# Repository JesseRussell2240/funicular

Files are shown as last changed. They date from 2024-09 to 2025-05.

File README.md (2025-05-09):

# funicular
Selfdriving R-pi code

**Establishing SSH From Laptop To Rpi**
1. Get IP of RPI should be like 192.168.#.###

2. Enable SSH on the Rpi
   -Open Terminal on the Rpi and type **"sudo raspi-config"** in the configuration menu go to "3. Interface      Options" and enable SSH
   -In CMD on laptop type "ssh rpi@rpi ip address found in step one" Ex. **"ssh rpi@192.168.#.###"**
   -If prompted with "WARNING: REMOTE HOST IDENTIFICATION HAS CHANGED" it means you have an existing key under that IP address, type "ssh-keygen -R ip address found in step one" Ex. **"ssh-keygen -R 192.168.#.###"** This will clear that key
   -Now try **"ssh rpi@192.168.#.###"** again, when prompted to continue connected type **"yes"**
   -When prompted for the password, enter the Rpis password you set when configuring Ex **"rpi_password"**
   -SSH should now be established

**Installing OpenCV in Terminal on Rpi**
1. In Terminal **"pip install opencv-python --break-system-package"**

**Installing PiCamera in Terminal on Rpi**
1. In Terminal **"pip install picamera --break-system-package"**

**Camera Unit Testing instructions**
**this needs confirming**
1. pip install picamera opencv-python

2. run unit testing code - python test_camera_module.py
After this is running you should see a window with a live camera feed.Type 'q' to exit.

**Preception unit testing instructions**
**This needs confirming**
1. pip install opencv-python numpy

2. run unit testing code - python test_perception_module.py
preception also has a main to test preception and cameras joint integration. Ensure camera module is successfull prior to moving on to preception.

This is to install flask and other for R-Pi server hosting website to control and recive video remotly
pip install flask flask-socketio opencv-python

ENSURE FLASK SERVER IS NOT IN DEBUG OR LIVESTREAM WILL NOT WORK

**Funicular Readme**

**------------------------------Python---------------------------------**

**App.py**<br>
App.py enables the flask-based web server and is responsible for all the data displayed on the web server and the controls within the web server. App.py sets up the flask server, enables and handles the frames of the Module 3 Wide PiCam (dependent on Autonomous or Manual Mode), enables, reads and graphs the BNO08X 9-DOF sensor data via I2C, and handles the flask routes for the webserver (landing_page, auto_mode, manual_mode, 3d_model, live_video & graphs)

**Machine Learning**<br>
For our ML model, we started by taking 100s of photos of our cones in various settings, configurations, and lighting, as well as some photos without cones. Once we had roughly 250 photos, we uploaded them to Roboflow (https://roboflow.com/), where we created our object class, cones, and manually selected the pixels containing cones. Once this was done, we used Roboflow to generate copies of each photo rotated, flipped, greyscales and inverted, bringing our total photos to about 1600. Once completed, we downloaded our dataset and yaml file. With our yaml created file, we then used the YOLO model 8 in Python to train on our dataset, running 100 epochs. Once this was completed, we received our best.pt file. Follow this tutorial to convert the .pt to a .hef and run it on Rpi’s Hailo Modules. https://www.youtube.com/watch?v=7pgSFgqo8gY
<br>
<br>
**-----------------------------Embedded--------------------------------**

**UART3.c**<br>
Sets up UART interface on USART3 for receiving motor control commands from an external Raspberry Pi. It handles the reception of direction, duty cycle, and turning values, parses them, and adjusts motor behaviour accordingly. The code includes an interrupt-driven approach for receiving data and sending responses back, allowing for continuous operation with real-time motor adjustments.

**DriveMotor_Breifing.c**<br>
The code configures and controls drive motors by setting up GPIO pins and timers to manage motor speed and direction. It uses PWM signals generated by Timer 8 for precise speed control and toggles GPIO pins for motor direction (forward, backward, or stop). The code provides functions to adjust both the speed (duty cycle) and direction of the turning and rear motors, allowing for real-time motor control in a robotic or motorized system.

**LimitSwitch.c**<br>
The code initializes and configures two limit switches (we run in series to PC5) to pins PC5 and PC6 of the STM32 microcontroller. The code triggers interrupts on the rising edge of the signals from these limit switches. When an interrupt is detected, the interrupt handler stops the turning motor (via the SetMotor function) and sets a flag indicating that a limit switch has been triggered. The interrupt flags are then cleared to allow further interrupts to be processed.

**Homing.c**<br>
The code implements a homing function for the turning motor using the limit switches and encoder to find the midpoint between two limit positions. It moves the motor left until the first limit switch is triggered, the encoder is reset, and the motor is reversed right to move towards the second limit switch. Once triggered, the motor is stopped, and the encoder value is recorded as the full turn value. The motor is then moved back toward the first limit switch, which continues until it reaches the midpoint of the full turn based on the encoder value. Once the midpoint is reached, the motor is stopped. The homing process ensures precise positioning with the help of the limit switches and encoder feedback.

**Encoder.c**<br>
The code initializes and configures the encoder interface using the TIM2 peripheral for motor pulse tracking. It enables clocks for the necessary GPIO ports and configures PA0 and PA1 as alternate function pins for TIM2 channels. TIM2 is set to encoder mode, which counts rising and falling edges from the input channels (CH1 and CH2). The encoder data is tracked through the TIM2 counter, which increments or decrements based on the motor's rotation direction. The encoder interface provides real-time position feedback, allowing motor position tracking.

**Pinouts**<br>
**Motors**<br>
PC2: Turning Motor Forward direction control (+ terminal)<br>
PC3: Turning Motor Reverse direction control (- terminal)<br>
PC10: Turning Motor PWM for speed control<br>
PB12: Rear Left Motor Forward direction control (+ terminal)<br>
PC4: Rear Left Motor Reverse direction control (- terminal)<br>
PC11: Rear Left Motor PWM for speed control<br>
PC1: Rear Right Motor Forward direction control (+ terminal)<br>
PC0: Rear Right Motor Reverse direction control (- terminal)<br>
PC12: Rear Right Motor PWM for speed control<br>

**Limit Switches**<br>
PC5: Left & right limit switch (wired in series) interrupts<br>

**Encoder**<br>
PA0: Encoder Channel 1 Pulse Input<br>
PA1 Encoder Channel 2 Pulse Input<br>

**UART**<br>
PB10: UART Transmit<br>
PB11: UART Receive<br>

**----------------------------Bill of Materials--------------------------**

**Raspberry Pi** (Tested on 8gb Rpi 5) https://www.pishop.ca/product/raspberry-pi-5-8gb/ 

**Raspberry Pi Ai Hat** https://www.pishop.ca/product/raspberry-pi-ai-hat-13-tops/ 

**Module 3 Wide PiCam** https://www.pishop.ca/product/raspberry-pi-camera-module-3-wide/

**BNO08X 9-DOF Sensor** https://www.adafruit.com/product/4754

**STM32F303RE** https://www.digikey.com/en/products/detail/stmicroelectronics/NUCLEO-F303RE/5052640 

**Quadrate Encoder Motor** https://www.amazon.ca/CHF-GM12-N20VA-Encoder-Reducer-Carbon-Popular/dp/B0DCRHDT71?th=1

**TT Motors** (Can buy from various sites, usually some good bundles on Amazon)

**Wheels & Tires** https://www.amazon.ca/SD-Tires-Off-Road-Wheel-Spokes/dp/B01DU1Q2Z2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

**Limit Switches** (Any normally open snap-action limit switches will do)

**Battery** (Any battery able to supply ~5A will do) 

**Voltage Regulators** (Any voltage regular capable of doing the supplied battery voltage down to 5V for the Rpi and 10V for the TT motors will do, we used) https://www.amazon.ca/dp/B076H3XHXP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 

TO DO
1. set up PI to host network
2. intgrate ML main and Flask server main
3. Get live cone frames into server
4. clean up GIT
5. Boot config for powerup booting Venv and server

**--------------------------------------------------------------------------------------------------------------------------<br>
-----------------------------------------------------Funicular By-------------------------------------------------------<br>
----------------------------------------------------Hayden & Jesse----------------------------------------------------<br>
----------------------------------------------------------2024----------------------------------------------------------<br>
--------------------------------------------------------------------------------------------------------------------------**

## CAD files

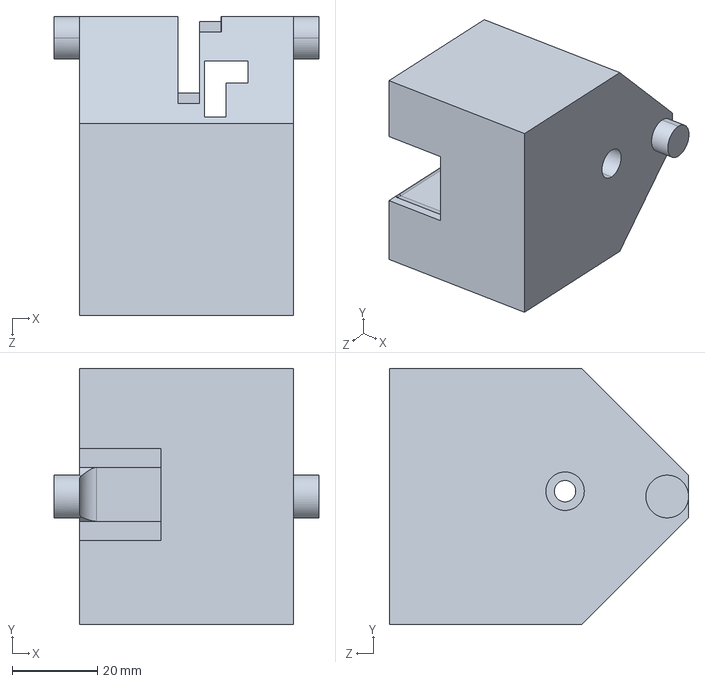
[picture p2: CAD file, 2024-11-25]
CAD/Solidworks/Print day 2/steering gearbox assembly.STEP
62.0 x 60.0 x 70.0 mm

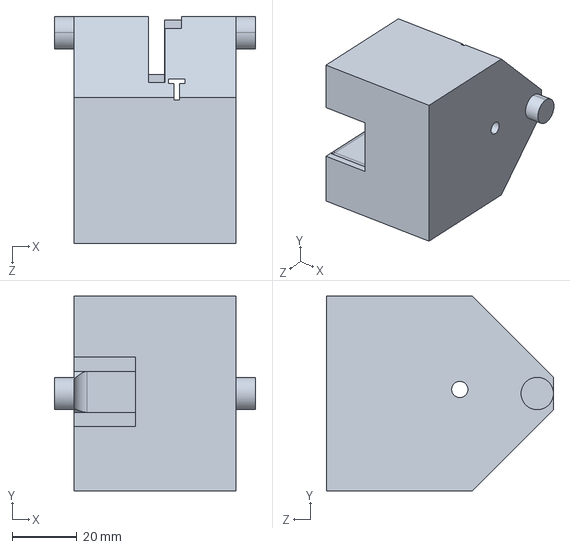
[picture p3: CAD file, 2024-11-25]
CAD/Solidworks/steering gearbox assembly.STEP
62.0 x 60.0 x 70.0 mm

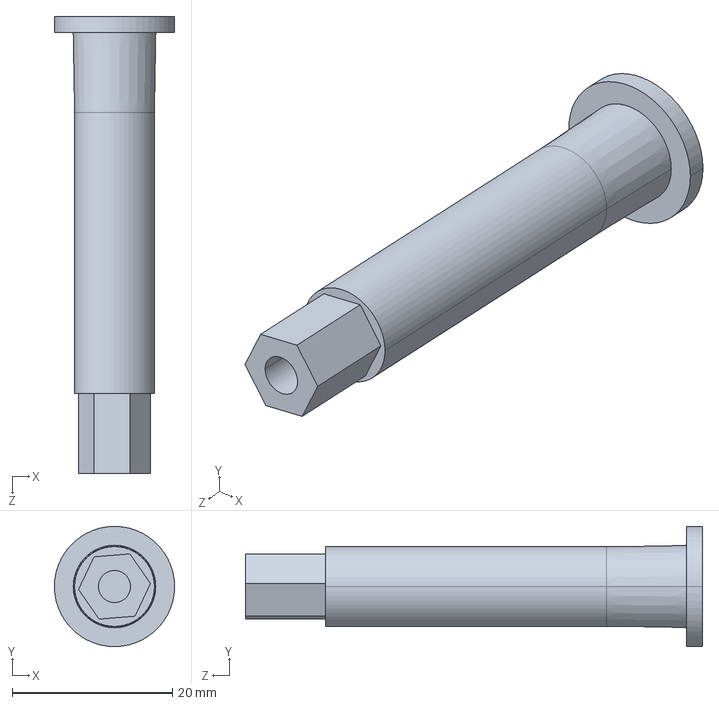
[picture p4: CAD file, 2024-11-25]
CAD/Solidworks/print day 2.2/rear bearing axel.STEP
15.0 x 15.0 x 57.0 mm

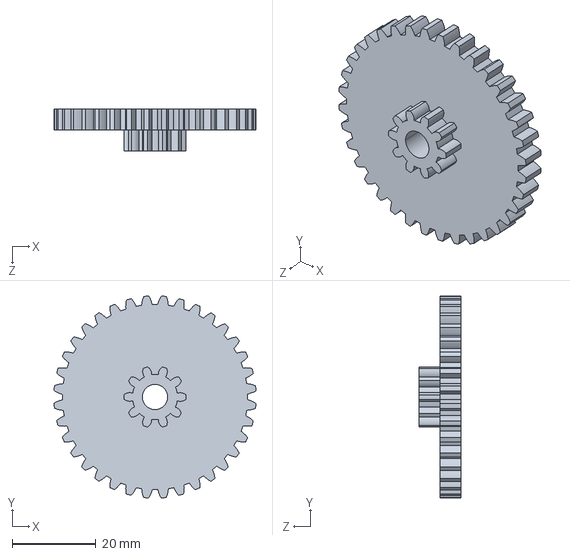
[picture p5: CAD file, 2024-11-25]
CAD/Solidworks/Print day 2/Reduction Gear.STEP
48.2 x 48.2 x 10.0 mm

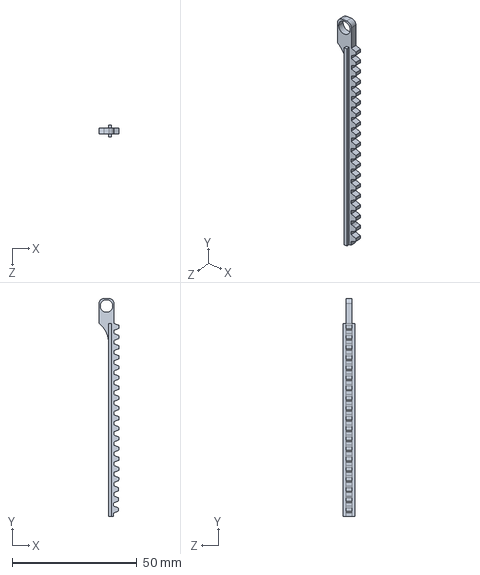
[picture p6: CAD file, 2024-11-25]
CAD/Solidworks/Rack Slidder.STEP
8.00 x 87.5 x 5.00 mm

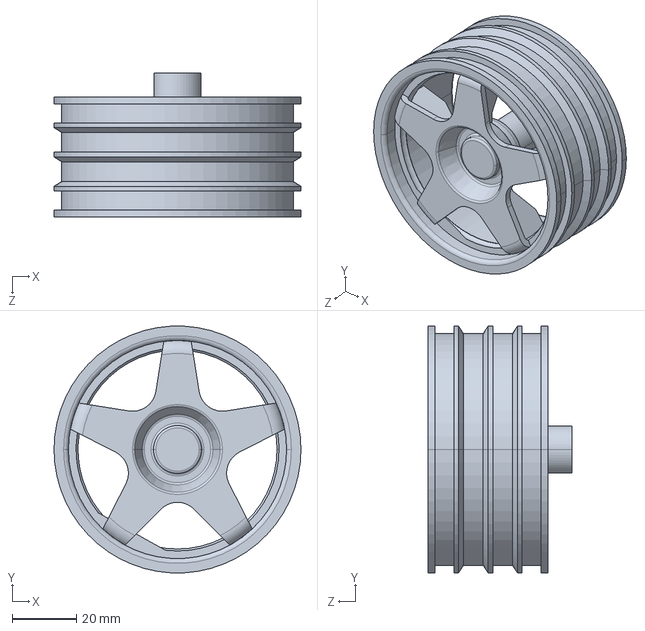
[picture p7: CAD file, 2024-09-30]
CAD/Solidworks/TireWheel/Rim.STEP
77.1 x 77.0 x 45.0 mm

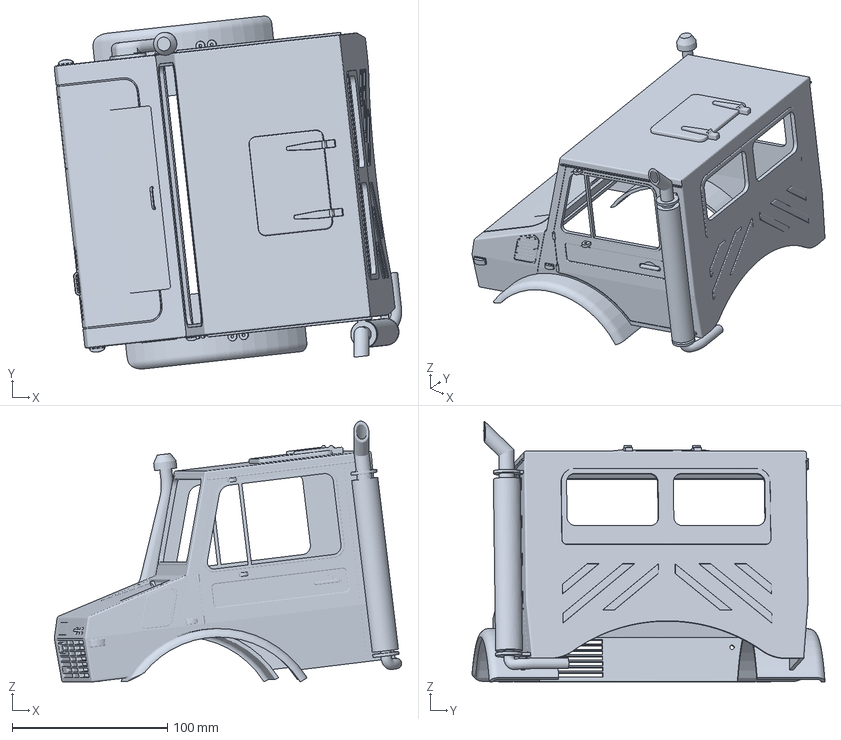
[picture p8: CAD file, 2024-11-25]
CAD/Solidworks/Unimog/Unimog.3mf
224.0 x 227.6 x 168.1 mm

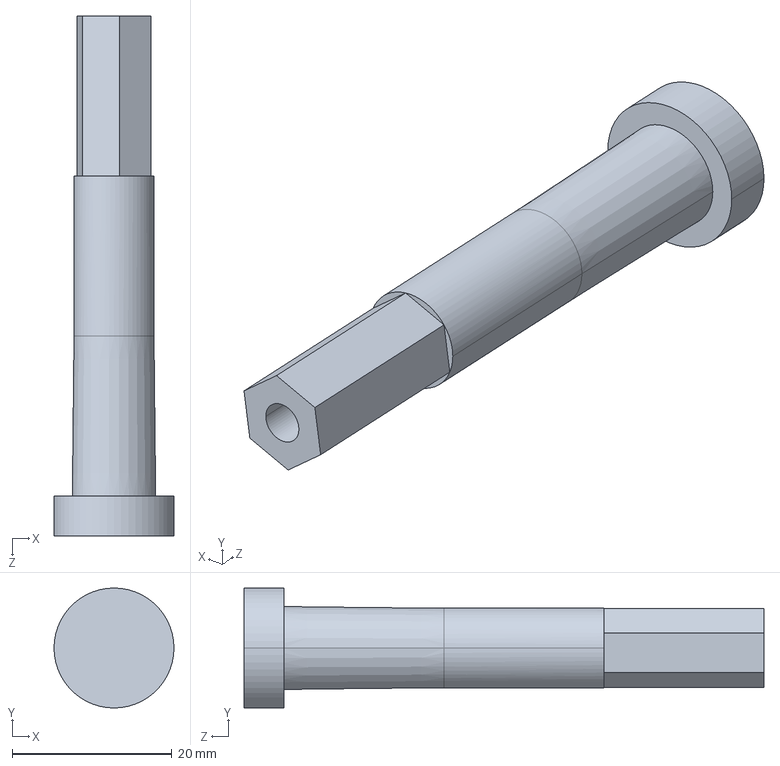
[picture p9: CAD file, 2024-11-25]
CAD/Solidworks/print day 2.2/front bearing axel part 1.STEP
15.0 x 15.0 x 65.0 mm

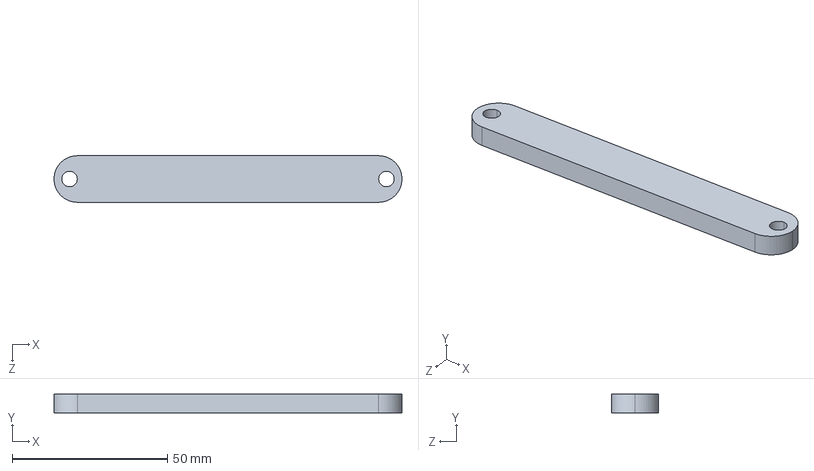
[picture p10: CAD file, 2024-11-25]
CAD/Solidworks/Print day 2/steering link.STEP
112.1 x 6.00 x 15.0 mm

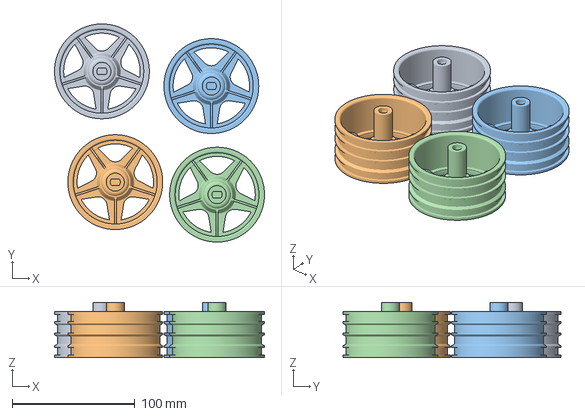
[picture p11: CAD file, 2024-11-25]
CAD/Solidworks/Printer Config.3mf
170.7 x 177.3 x 45.0 mm
Rim.STEP x 4

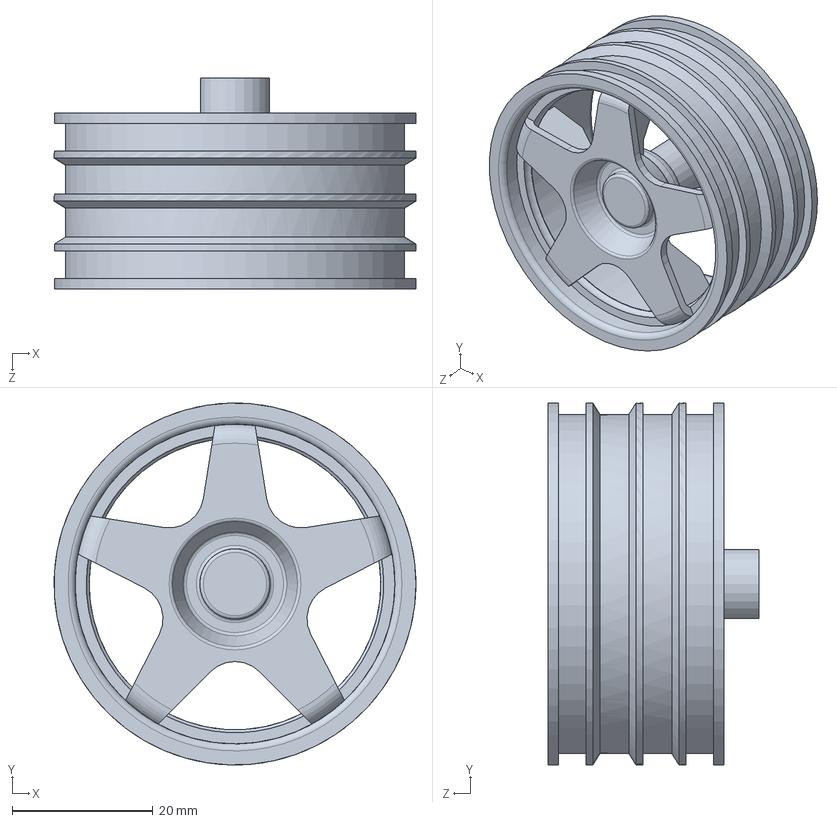
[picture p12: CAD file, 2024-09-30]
CAD/Solidworks/TireWheel/Fillet6.SLDPRT
51.4 x 51.4 x 30.0 mm

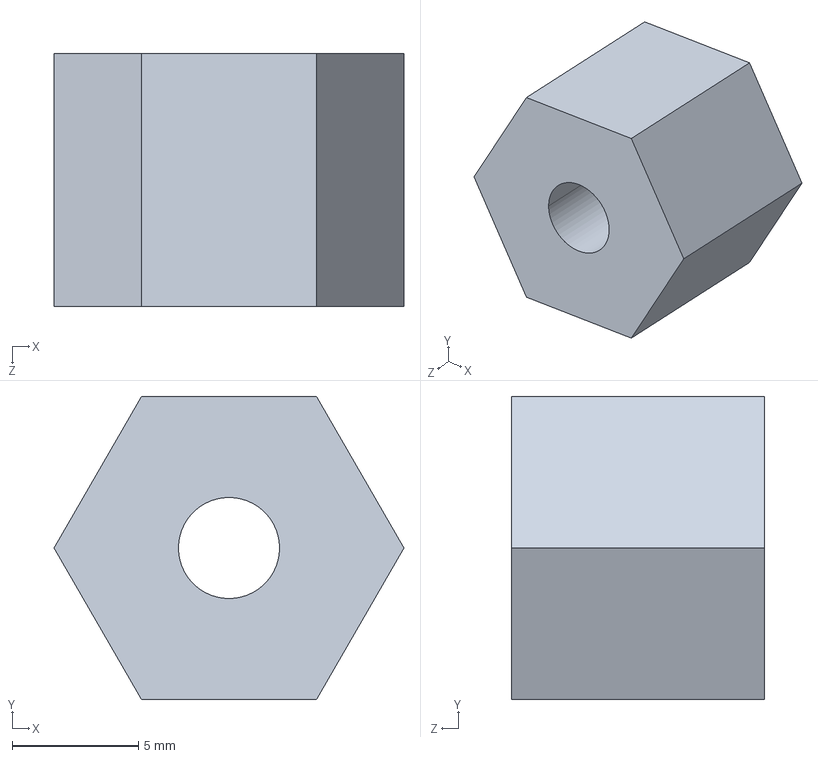
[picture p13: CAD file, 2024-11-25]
CAD/Solidworks/print day 2.2/wheel adapter.STEP
13.9 x 12.0 x 10.0 mm

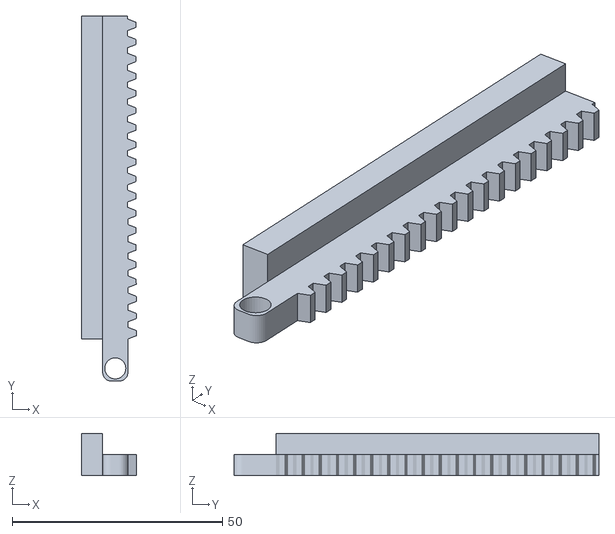
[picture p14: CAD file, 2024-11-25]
CAD/Solidworks/Print day 2/Assem1 - Assem1.STEP-1 MirrorRack Slidder.STEP-1.STL
13.0 x 86.8 x 10.00

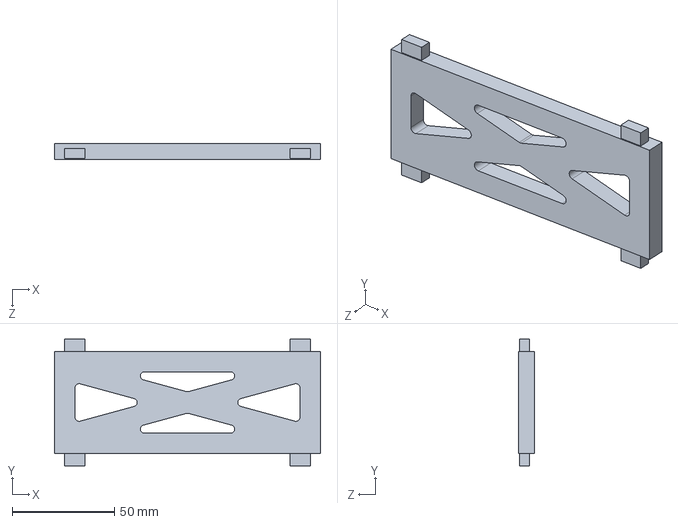
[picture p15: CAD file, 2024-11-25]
CAD/Solidworks/Side Support.STEP
130.0 x 62.0 x 8.00 mm

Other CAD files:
CAD/Solidworks/DC Motor Gearbox.SLDASM
CAD/Solidworks/funicular.SLDASM
CAD/Solidworks/Steering Assembily.SLDASM
CAD/Solidworks/print day 2.2/steering link.STEP
CAD/Solidworks/Boss-Extrude5.SLDPRT
CAD/Solidworks/Chass.SLDPRT
CAD/Solidworks/Encloser.SLDPRT
CAD/Solidworks/Gearing Test.SLDPRT
CAD/Solidworks/Knuckle.SLDPRT
CAD/Solidworks/MirrorRack Slidder.SLDPRT
CAD/Solidworks/Motor Pinion.SLDPRT
CAD/Solidworks/Motor Pinion.STEP
CAD/Solidworks/Print day 2/Assem1 - Assem1.STEP-1 Rack Slidder_2.STEP-1.STL
CAD/Solidworks/Print day 2/Assem1.SLDASM
CAD/Solidworks/Print day 2/Assem1.STEP
CAD/Solidworks/Print day 2/ParkingCone.3mf
CAD/Solidworks/Print day 2/ParkingCone.STEP
CAD/Solidworks/Print day 2/Rack Slidder.STEP
CAD/Solidworks/Print day 2/front bearing axel part 1.STEP
CAD/Solidworks/Print day 2/rear bearing axel.SLDPRT
CAD/Solidworks/Print day 2/rear bearing axel.STEP
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

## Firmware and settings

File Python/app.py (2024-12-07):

from flask import Flask, render_template, jsonify, Response, request
import threading
import time
import json
import board
import busio
import adafruit_bno08x
from adafruit_bno08x.i2c import BNO08X_I2C
from picamera2 import Picamera2
import cv2
from io import BytesIO
from flask_cors import CORS
from cone_detection import detect_cones
from controllers.auto_control import control_routes
import serial
import threading

auto_flag = False
auto_lock = threading.Lock()

# Flask setup
app = Flask(__name__)
CORS(app)
app.register_blueprint(control_routes, url_prefix='/control')  # Register with a prefix (optional)

# Initialize the camera
picam2 = Picamera2()
picam2.configure(picam2.create_video_configuration(main={"size": (640, 480)}))

# Global variables for sensor data
gyro_data = {'gyro_x': 0.0, 'gyro_y': 0.0, 'gyro_z': 0.0}
acc_data = {'acc_x': 0.0, 'acc_y': 0.0, 'acc_z': 0.0}
vel_data = {'vel_x': 0.0, 'vel_y': 0.0, 'vel_z': 0.0}
last_time = time.time()

# Set up I2C connection for the sensor
i2c = busio.I2C(board.SCL, board.SDA, frequency=400000)  # 400kHz recommended for BNO085
bno = BNO08X_I2C(i2c)

# Enable sensor features
bno.enable_feature(adafruit_bno08x.BNO_REPORT_ACCELEROMETER)
bno.enable_feature(adafruit_bno08x.BNO_REPORT_GYROSCOPE)

# Add a threading lock
data_lock = threading.Lock()

# Serial connection configuration
SERIAL_PORT = "/dev/serial0"  # Serial port for UART (change if needed)
BAUD_RATE = 9600              # Common baud rate for UART



# Initialize the serial connection
ser = serial.Serial(SERIAL_PORT, BAUD_RATE, timeout=1)

stmIsHome = False            # Homing flag
steering_center = 30          # Steering center position
steering_max = 60             # Maximum turning value LEFT
steering_min = 0             # Minimum turning value 
half_steering_left = 15      # Half turn left position
half_steering_right = 45     # Half turn right position
full_power = 60              # Full forward/backward power
half_power = 40              # Half power


def transmit(data):
    global stmIsHome, steering_center, steering_max

    try:
        # Ensure the serial port is open
        if not ser.is_open:
            ser.open()

        # Check if the system is homed
        if not stmIsHome:
            # Send the homing command
            homing_packet = "* 00 30\n"
            ser.write(homing_packet.encode())  # Convert string to bytes
            print(f"Transmitting homing packet: {homing_packet}")
            time.sleep(1)
            # Receive the maximum turning value
            received_data = receive()
            print(f"GOT {received_data}")
            if received_data:
                try:
                    # Parse the received maximum turning value
                    steering_max = int(received_data.strip())
                    steering_center = steering_max // 2  # Calculate the steering center
                    
                    steeringIncrement = steering_center // 2
                    half_steering_left = steering_center - steeringIncrement
                    half_steering_right = steering_center + steeringIncrement
                    
                    stmIsHome = True  # Update the homing flag
                    print(f"Received max turning: {steering_max}, Steering center: {steering_center}")
                    
                except ValueError:
                    print("Error parsing received max turning value.")
                    return
            else:
                print("No response received for homing packet.")
                return

        # Transmit the provided data over UART
        ser.write(data.encode())  # Convert string to bytes
        print(f"Transmitting: {data}")

        # Receive response after transmission (you can modify this as per your protocol)
          # Function to read data from serial port

        while True:
            # Simulate receiving data (replace this with actual data retrieval logic)
            #received_data = input("Enter received data for testing: ")  # Example for testing
            received_data = receive()
            # Check if the received data contains "1"
            if received_data and "1" in received_data:  # Replace 'expected_response' with your actual check
                print("Handshake confirmed")
                break  # Exit the loop once the condition is met
            else:
                print("Error in transmission, waiting...")
                
    except serial.SerialException as e:
        print(f"Error with serial connection: {e}")
    except Exception as e:
        print(f"General error: {e}")
    finally:
        # Optionally, close the serial port after transmission
        ser.close()

def receive():
    try:
        # Read available data from the serial buffer
        received_data = ser.read(ser.in_waiting or 1).decode('utf-8')  # Read data
        return received_data if received_data else None
    except serial.SerialException as e:
        print(f"Error reading data: {e}")
        return None

# Movement control functions
def move_forward():
    steering = steering_center  # No turn
    packet = f"+ {full_power:02} {steering_center}"
    transmit(packet + '\n')

def move_backward():
    steering = steering_center  # No turn
    packet = f"- {full_power:02} {steering_center}"
    transmit(packet + '\n')

def move_stop():
    speed = 0  # No movement
    packet = f"| {speed:02} {steering_center}"
    transmit(packet + '\n')
    
def move_left():
    packet = f"+ {half_power:02} {steering_min + 7}"
    transmit(packet + '\n')
    #time.sleep(1)
    #move_stop()

def move_right():
    packet = f"+ {half_power:02} {steering_max - 7}"
    transmit(packet + '\n')
    #time.sleep(1)
    #move_stop()

def move_left_half():
    packet = f"+ {half_power:02} {half_steering_left}"
    transmit(packet + '\n')
    #time.sleep(1)
    #move_stop()

def move_right_half():
    packet = f"+ {half_power:02} {half_steering_right}"
    transmit(packet + '\n')
    #ime.sleep(1)
    #move_stop()
    
auto_flag = False
    
def drive_to_target(center_x, center_y, cone_size):
    """Move the robot to the center of the two cones (target coordinates)."""
    print(f"Driving to coordinates: {center_x}, {center_y} with cone size: {cone_size}")

    # Calculate the proportional error in the x-direction
    target_center_x = 320  # Assuming the center of the camera frame is at 320 (horizontal center)
    error_x = center_x - target_center_x

    # Set the proportional gain for left/right movement
    Kp_x = 0.10  # You may need to tune this value to adjust responsiveness
    turn_speed = Kp_x * error_x  # This determines how fast to turn (proportional to the error)

    # Set the proportional gain for speed (based on the size of the cone)
    Kp_size = 0.5  # You may need to tune this value for better control
    #speed = Kp_size * cone_size  # This adjusts speed based on the cone size
    #speed = 65
    speed = Kp_size * full_power
    
    # Limit the speed for safety
    max_speed = 99
    if speed > max_speed:
        speed = max_speed
    #print(f"speed: {speed}")
    print(f"turn factor: {turn_speed}")

        
     # Determine direction based on error_x
    if error_x < -15:  # If the error is negative, it means the target is to the left
        turn_value = max(steering_min, min(steering_max, int(steering_center + turn_speed)))  # Clamp between 5 and 55
        packet = f"+ {int(speed)} {turn_value}"  # Turn left with proportional speed
        transmit(packet + '\n')
    elif error_x > 15:  # If the error is positive, it means the target is to the right
        turn_value = max(steering_min, min(steering_max, int(steering_center + turn_speed)))
        packet = f"+ {int(speed)} {turn_value}"  # Turn right with proportional speed
        transmit(packet + '\n')
    else:
        # If the target is centered, just move forward
        packet = f"+ {int(speed)} 30"  # Move forward
        transmit(packet + '\n')



auto_flag = False
auto_lock = threading.Lock()
     
def autonomous_loop():
    """Function to run autonomous mode in a separate thread."""
    global auto_flag
    json_file_path = '/home/rpi/Desktop/Beta/Python/hailo-rpi5-examples/cone_detection.json'

    while True:
        with auto_lock:
            if not auto_flag:
                break

        try:
            # Open and read the JSON file
            with open(json_file_path, 'r') as json_file:
                data = json.load(json_file)

            # Extract cone data
            red_cone = data.get("largest_red_cone", {"center": [0, 0], "area": 0})
            blue_cone = data.get("largest_blue_cone", {"center": [0, 0], "area": 0})

            # Extract properties
            red_x, red_y = red_cone['center']
            blue_x, blue_y = blue_cone['center']
            red_area = red_cone.get('area', 0)
            blue_area = blue_cone.get('area', 0)

            if red_area > 0 and blue_area > 0:
                # Case: Both cones are non-zero
                center_x = (red_x + blue_x) / 2
                center_y = (red_y + blue_y) / 2
                avg_area = (red_area + blue_area) / 2
                print("Both cones detected with non-zero area. Driving to target.")
                drive_to_target(center_x, center_y, avg_area)

            elif red_area > 0 or blue_area > 0:
                # Case: One cone is non-zero
                if red_area > 0:
                    print("Single red cone detected.")
                    cone_x = red_x
                else:
                    print("Single blue cone detected.")
                    cone_x = blue_x

                screen_midpoint = 320  # Adjust based on your screen resolution
                if cone_x < screen_midpoint:
                    if red_area > 0:
                        print("Red cone on the left. Turning right half.")
                        move_right_half()
                    else:
                        print("Blue cone on the left. Turning left full.")
                        move_left()
                else:
                    if red_area > 0:
                        print("Red cone on the right. Turning right full.")
                        move_right()
                    else:
                        print("Blue cone on the right. Turning left half.")
                        move_left_half()
            else:
                # Case: Both cones have zero values
                print("No valid cones detected. Stopping the car.")
                move_stop()

        except FileNotFoundError:
            print(f"JSON file not found: {json_file_path}")
        except json.JSONDecodeError:
            print("Error decoding JSON file. Ensure it is correctly formatted.")
        except KeyError as e:
            print(f"Unexpected key error: {e}")

        time.sleep(0.1)    
   
# Function to update sensor data
def update_sensor_data():
    global gyro_data, acc_data, vel_data, last_time
    while True:
        try:
            # Fetch gyroscope data
            gyro_x, gyro_y, gyro_z = bno.gyro
            new_gyro_data = {
                'gyro_x': gyro_y,
                'gyro_y': gyro_z,
                'gyro_z': gyro_x
            }

            # Fetch acceleration data
            acc_x, acc_y, acc_z = bno.acceleration
            new_acc_data = {
                'acc_x': acc_x,
                'acc_y': acc_y,
                'acc_z': acc_z
            }

            # Calculate velocity data
            current_time = time.time()
            dt = current_time - last_time
            last_time = current_time
            new_vel_data = {
                'vel_x': acc_x * dt,
                'vel_y': acc_y * dt,
                'vel_z': acc_z * dt
            }

            # Update global variables with lock
            with data_lock:
                gyro_data = new_gyro_data
                acc_data = new_acc_data
                vel_data = new_vel_data

            time.sleep(0.1)
        except Exception as e:
            print(f"Error in sensor thread: {e}")
            time.sleep(1)

# Function to generate frames for the video feed
def generate_frames():
    global autonomous_page  # Declare the flag as global
    while True:
        try:
            frame = picam2.capture_array()
            
            frame = cv2.cvtColor(frame, cv2.COLOR_BGR2RGB)  # Convert to RGB
            
            # Convert the frame to JPEG
            stream = BytesIO()
            success, encoded_image = cv2.imencode('.jpeg', frame)
            if success:
                stream.write(encoded_image.tobytes())
                stream.seek(0)

            yield (b'--frame\r\n'
                   b'Content-Type: image/jpeg\r\n\r\n' + stream.read() + b'\r\n')
        except Exception as e:
            print(f"Error in generating frames: {e}")
            time.sleep(1)

@app.route('/control/move', methods=['POST'])
def move():
    global movement_status
    data = request.json
    direction = data.get('direction', 'stop')
    movement_status = direction

    # Print button press to the console
    print(f"[MOVE] Button pressed: {direction.capitalize()}")

    # Perform the movement action
    if direction == "forward":
        move_forward()
    elif direction == "backward":
        move_backward()
    elif direction == "left":
        move_left()
    elif direction == "right":
        move_right()
    else:
        move_stop()

    return jsonify({"status": f"Moving {direction}"}), 200

@app.route('/control/bluetooth', methods=['POST'])
def bluetooth():
    global bluetooth_enabled
    action = request.json.get('action', 'disable')
    bluetooth_enabled = (action == 'enable')
    status = "enabled" if bluetooth_enabled else "disabled"
 
    # Print button press to the console
    action_text = "Enable Bluetooth" if bluetooth_enabled else "Disable Bluetooth"
    print(f"[BLUETOOTH] Button pressed: {action_text}")
 
    if bluetooth_enabled:
        try:
            import pygame
            pygame.init()
            pygame.joystick.init()
 
            if pygame.joystick.get_count() == 0:
                print("[BLUETOOTH] No controller detected.")
                return jsonify({"status": "error", "message": "No controller detected"}), 400
 
            controller = pygame.joystick.Joystick(0)
            controller.init()
 
            print("[BLUETOOTH] PS4 controller connected.")
 
            running = True
            while running and bluetooth_enabled:
                pygame.event.pump()
 
                # Left joystick for steering
                left_x = controller.get_axis(0)

                

                # Determine direction and movement based on joystick and triggers
                direction = "|"  # Default direction (Neutral)
                pwm_percentage = 0
                steering_angle = steering_center
                
                # Determine movement direction based on the joystick
                if left_x <= -0.4:
                    steering_angle = int(30 + (left_x * 30))
                    steering_angle = max(7, min(53, steering_angle))  # Clamp between 7 and 53
                elif left_x >= 0.4:
                    steering_angle = int(30 + (left_x * 30))
                    steering_angle = max(10, min(50, steering_angle))  # Clamp between 7 and 53

                # Handle triggers for forward/backward movement
                left_trigger = controller.get_axis(2)
                right_trigger = controller.get_axis(5)

                if left_trigger > 0:  # Forward movement
                    pwm_percentage = int(60 + (left_trigger * 30))  # Forward speed calculation
                    direction = "-"  # Forward direction
                elif right_trigger > 0:  # Backward movement
                    pwm_percentage = int(60 + (right_trigger * 30))  # Backward speed calculation
                    direction = "+"  # Backward direction
                else:  # No trigger pressed
                    pwm_percentage = 0  # No movement
                    direction = "|"  # Stopped

                # Construct the transmit packet
                packet = f"{direction} {pwm_percentage} {steering_angle}"
                transmit(packet + '\n')
                # Transmit the constructed packet
                #print(f"[BLUETOOTH] Transmit Packet: {transmit_packet}")
 
        except Exception as e:
            print(f"[BLUETOOTH] Error: {str(e)}")
            return jsonify({"status": "error", "message": str(e)}), 500
 
    return jsonify({"status": f"Bluetooth {status}"}), 200



# Flask route to provide sensor data
@app.route('/sensor_data')
def get_sensor_data():
    with data_lock:
        return jsonify(gyro_data)

@app.route('/graph_data')
def get_graph_data():
    with data_lock:
        data = {
            "acc_data": acc_data,
            "vel_data": vel_data
        }
    return jsonify(data)
    
# Route for live camera feed
@app.route('/video_feed')
def video_feed():
    try:
        picam2.start()  # Start the camera when the video feed route is called
    except Exception as e:
        print(f"Camera error while starting: {e}")
    return Response(generate_frames(), mimetype='multipart/x-mixed-replace; boundary=frame')

# Main route for the Flask web app
@app.route('/')
def landing_page():
    try:
        picam2.stop()  # Stop the camera when landing page is called
    except Exception as e:
        print(f"Camera error while stopping: {e}")
    return render_template('landing_page.html')

@app.route('/auto')
def auto_mode():
    global autonomous_page
    autonomous_page = True
    try:
        picam2.stop()  # Stop the camera when entering auto mode
    except Exception as e:
        print(f"Camera error while stopping: {e}")
    return render_template('auto_mode.html')

@app.route('/manual')
def manual_mode():
    global autonomous_page
    autonomous_page = False
    try:
        picam2.stop()  # Stop the camera when entering manual mode
    except Exception as e:
        print(f"Camera error while stopping: {e}")
    return render_template('manual_mode.html')

@app.route('/3d')
def model_3d():
    try:
        picam2.stop()  # Stop the camera when 3D model page is called
    except Exception as e:
        print(f"Camera error while stopping: {e}")
    return render_template('3d_model.html')

@app.route('/video')
def live_video():
    return render_template('live_video.html')

@app.route('/graphs')
def graphs():
    try:
        picam2.stop()  # Stop the camera when graph page is called
    except Exception as e:
        print(f"Camera error while stopping: {e}")
    return render_template('graphs.html')

@app.route('/control/start_autonomous', methods=['POST'])
def start_autonomous():
    global auto_flag
    with auto_lock:
        if auto_flag:
            return jsonify({"message": "Autonomous mode is already running"}), 400
        auto_flag = True
    
    threading.Thread(target=autonomous_loop, daemon=True).start()
    print("Start Autonomous Mode triggered!")
    return jsonify({"message": "Autonomous mode started"}), 200

@app.route('/control/stop_autonomous', methods=['POST'])
def stop_autonomous():
    global auto_flag
    with auto_lock:
        auto_flag = False
    print("Stop Autonomous Mode triggered!")
    move_stop()  # Stop the robot
    return jsonify({"message": "Autonomous mode stopped"}), 200

# Start the sensor data updating thread
if __name__ == "__main__":
    sensor_thread = threading.Thread(target=update_sensor_data, daemon=True)
    sensor_thread.start()
    app.run(host='0.0.0.0', port=5000, debug=False)

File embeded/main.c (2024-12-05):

#include "stm32f303xe.h"
#include "SysClock.h"
#include <stdio.h>
#include "UART3.h"
#include "DriveMotor.h"
#include "LimitSwitch.h"
#include "Encoder.h"
#include "Homing.h"
#include "Auto_Driving.h"



#define MAX_UART3_BUFSIZ 60



extern char rxBuffer[MAX_UART3_BUFSIZ];




int main(void){
	
	
	
	
	 System_Clock_Init(); // Call the system clock initialization from SysClock.c
   SystemCoreClockUpdate(); // Update the system core clock variable
   
	 DriveMotor_Init(); //motor initialization
	 StopAllMotors(); //stop all motors for start
   LimitSwitch_Init(); //Limit Switch init
 	 Encoder_Init(); //Encoder init
	 homing_Init(); //Home the steering rack
	
	 UART3_Init();

		
			
   for(;;){
		 

			
			
			
		
	
	
	}

}

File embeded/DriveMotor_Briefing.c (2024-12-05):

// Drive Motor Module Source File
	///////////////////////////////////////////////////////////////////
	/////////////////////MOTOR DRIVER//////////////////////////////////
	///////////////////Hayden F & Jesse R/////////////////////////////
  //////////////////////////2024///////////////////////////////////

#include "DriveMotor.h"
#include "utility.h"
//#include "UART3.h"

// Drive Motor Configuration Parameters

//////////Turning Motor///////////////
// PC 2 +
// PC 3 -
// PC 10 PWM


//////////Rear Left///////////////////
// PB 12 +
// PC 4  -
// PC 11 PWM

//////////Rear Right
// PC 1 +
// PC 0 -
// PC 12 PWM


//
// - Direction Control Truth Table
//     STOP   FWD	RWD   UNDEFINED
// (A)  0      1     0      1     
// (B)  0      0     1      1
static uint16_t currentDutyCycle = 0;

void DriveMotor_Init(void)
{
	//CLEAR_BITS(RTC->TAFCR, RTC_TAFCR_PC13MODE);
	

	SET_BITS(RTC->TAFCR, RTC_TAFCR_PC13MODE);
		 
	
	// Enable GPIO Clock
		 ENABLE_CLOCKx(C);
	   ENABLE_CLOCKx(B);

	

	///////////////////////////////////////////////////////////////////
	////////////////Turning MOTORS INIT////////////////////////////////
	///////////////////////////////////////////////////////////////////
	
	// Configure Motor Control Pins 
	//  For Direction Control, just ordinary GPIO configurations
	//    MODE = Output
		
		 MODER_SET(C,3,MODER_GP);
		 MODER_SET(C,2,MODER_GP);
	
	//    Output Type = Push Pull

	  GPIO_OTYPER_SET(C,3,OTYPER_PP);
	  GPIO_OTYPER_SET(C,2,OTYPER_PP);
	
	//    Pull-up / Pull-down = No Pull
	
		PUPDR_SET(C,3,PUPDR_NP);
		PUPDR_SET(C,2,PUPDR_NP);
		
	//    Initial Output Value should be set to 0 (STOP by default)
		
		CLEAR_BITS( GPIOC->ODR, GPIO_ODR_3);
		CLEAR_BITS( GPIOC->ODR, GPIO_ODR_2);
		
	//  For Speed Control, connect TIM8 channels to PC10 and PC11 with the following configurations
	//	  MODE = Alternative Function 4

		MODER_SET(C,10,MODER_AF);
		GPIO_AFRH(C,2,4UL);

		
	//    Output Type = Push Pull

  	GPIO_OTYPER_SET(C,10,OTYPER_PP);
		
	//    Pull-up / Pull-down = No Pull
	
		PUPDR_SET(C,10,PUPDR_NP);
		
	//  PC10 will be connected to TIM8 channel 1N (complemented output)
	//  PC11 will be connected to TIM8 channel 2N (complemented output)
	
	

		//////////////////////////////////////////////////////////////////
	////////////////REAR MOTORS INIT///////////////////////////////////
	//////////////////////////////////////////////////////////////////
	
		
	// Configure Motor Control Pins 
	//  For Direction Control, just ordinary GPIO configurations
	//    MODE = Output
		 MODER_SET(B,12,MODER_GP);
		 MODER_SET(C,4,MODER_GP);
		 MODER_SET(C,1,MODER_GP);
		 MODER_SET(C,0,MODER_GP);
	
	//    Output Type = Push Pull
		GPIO_OTYPER_SET(B,12,OTYPER_PP);
  	GPIO_OTYPER_SET(C,4,OTYPER_PP);
	  GPIO_OTYPER_SET(C,1,OTYPER_PP);
	  GPIO_OTYPER_SET(C,0,OTYPER_PP);
	
	//    Pull-up / Pull-down = No Pull
		PUPDR_SET(B,12,PUPDR_NP);
		PUPDR_SET(C,4,PUPDR_NP);
		PUPDR_SET(C,1,PUPDR_NP);
		PUPDR_SET(C,0,PUPDR_NP);
		
	//    Initial Output Value should be set to 0 (STOP by default)
		CLEAR_BITS( GPIOB->ODR, GPIO_ODR_12);
		CLEAR_BITS( GPIOC->ODR, GPIO_ODR_4);
		CLEAR_BITS( GPIOC->ODR, GPIO_ODR_1);
		CLEAR_BITS( GPIOC->ODR, GPIO_ODR_0);
		
	//  For Speed Control, connect TIM8 channels to PC9 and PC12 with the following configurations
	//	  MODE = Alternative Function 4
		MODER_SET(C,12,MODER_AF);
		MODER_SET(C,11,MODER_AF);
		GPIO_AFRH(C,4,4UL);
		GPIO_AFRH(C,3,4UL);
		
	//    Output Type = Push Pull
		GPIO_OTYPER_SET(C,12,OTYPER_PP);
  	GPIO_OTYPER_SET(C,11,OTYPER_PP);
		
	//    Pull-up / Pull-down = No Pull
		PUPDR_SET(C,12,PUPDR_NP);
		PUPDR_SET(C,11,PUPDR_NP);
		
		
		

		

		
		///////////////////////////////////////////////////////////////////
	////////////////MOTORS PWM////////////////////////////////////
	//////////////////////////////////////////////////////////////////
	

	
	// Next, Configure Timer 8 for CH1N and CH2N - Mostly like Servo with 2 exceptions 
	// 1. Turn o Timer 8
	  SET_BITS(RCC->APB2ENR, RCC_APB2ENR_TIM8EN);
		
	// 2. Program Timer 8 prescaler to count in microseconds
		//You need -1 to allow the timer start sequence (mandatory)
		 TIM8->PSC = SystemCoreClock / 1000000 - 1;
		 
	// 3. Set TIM8 to upcounting mode (MANDATORY!! because TIM8 default mode can be something else)
		// [DIFFERENT!] This is different from TIM15 in Servo Lab because TIM15 only supports upcounting
		CLEAR_BITS(TIM8->CR1, TIM_CR1_DIR);
		
	// 4. Set the TIM8 reload value to 1000 us period (Remember -1 because it's repeating)
		TIM8->ARR = 1000 - 1;
			
	// 5. Enable TIM8 ARR preload
		SET_BITS(TIM8->CR1, TIM_CR1_ARPE);
		
	// 6. Set TIM8 main output enabled
	  SET_BITS(TIM8->BDTR, TIM_BDTR_MOE);
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

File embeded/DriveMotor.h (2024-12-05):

#include "utility.h"
#include "stm32f303xe.h"

#define motorFrontLeft  0UL
#define motorFrontRight 1UL
#define motorRears      2UL
#define motorTurning    3UL

#define DIR_FWD    0UL
#define DIR_BWD    1UL
#define DIR_STOP   2UL

#define DIR_LEFT   3UL
#define DIR_RIGHT  4UL

void DriveMotor_Init(void);
void SetMotorSpeed( uint8_t motor, uint16_t dutyCycle );
void SetMotorDir( uint8_t motor, uint8_t dir );
void SetMotor( uint8_t motor, uint8_t dir, uint16_t dutyCycle );
void SweepMotor( uint8_t motor, uint16_t dutyCycle);
void TurnMotor(uint16_t turningAngle );
void StopAllMotors(void);

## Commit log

2024-09-24 init of camera and preception
    fixed included. Refactored spelling mistakes in color vs colour
2024-09-30 CAD for frame
    [Boss-Extrude5.SLDPRT, Chass.SLDPRT, DC Motor Gearbox.SLDASM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]
2024-10-01 Created embeded subfolder
    Created uvision project and added generic files
    [Rack Slidder.SLDPRT, Rim.SLDPRT, Steering Assembily.SLDASM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]
2024-10-01 created limit switch
2024-10-03 Created LimitSwitch Code base and Uart3 both in interrupt
2024-10-03 UART Ping
    Uart ping code
2024-10-04 IDEK
    played with UART3
2024-10-04 Changed UARTPingATT2
    Transmit random num
2024-10-04 Update UARTPingAtt2.py
    Chaged back to a char because by uart code doesnt do nums rn
2024-10-05 Create UARTPingString.py
    Testing UART String comms
2024-10-05 UARTPingAtt2
    Added custom user messages so i can swith between transferring chars and string without having to push new programs while i trouble shoot
2024-10-05 UART & Pi sending strings back n forth
2024-10-07 update to cad due to assembly
    [DC Motor Gearbox.SLDASM, Knuckle.SLDPRT, MirrorRack Slidder.SLDPRT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]
2024-10-07 updated app.py to resolve r-pi specific issue
    [app.py]
2024-10-11 Encoder
    Encoders telling direction ish
2024-11-01 Update app.py
    This should be last working copy with midpoint and left right and steering angle
